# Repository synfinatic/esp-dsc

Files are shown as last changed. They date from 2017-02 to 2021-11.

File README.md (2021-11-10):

# ESP-DSC: Digital Setting Circles for ESP-12E/F

## About

Low cost alternative to my original Digital Setting Circles project the
[Teensy-DSC](https://github.com/synfinatic/teensy-dsc/).  This new design
uses the cheap ESP-12E/F WiFi enabled microcontroller which saves about 60% 
of the original price (~$40 vs ~$100).

I'm also planing to include the necessary .STL files so you can 3D print
the appropriate enclosure for the board.

More information about this project is available [on my website](https://synfin.net/sock_stream/tag/esp-dsc).

## v1.2 Status

 * Design PCB (complete!)
 * Port over the TeensyDSC code to the ESP-12 (complete!)
 * Verify that the ESP-12E is capable of handeling 2.5K PPR/10K count encoders (complete!)
 * Verify that the ESP-12E is capable of handeling 10K PPR/40K count encoders (failed!)
 * Create the necessary STL files to 3D print an enclosure for the board (complete!)
 * Major board change between v1.0 and v1.1- different pins used!

## v2.0 Status 
 * Redesign PCB for better performance  (TBD)
 * Update code based on new design (TBD)
 * Verify that the ESP-12E is capable of handeling 10k encoders (TBD)

## Performance

So a quick word about performance.  There are a number of people who claim that 
the ESP-12E has enough horsepower for two 2500PPR (10K after quadurature decoding) 
encoders.  One person told me they saw some errors, but they were small and 
likely caused by their mount.  This didn't seem very scientific to me, so I ran 
some tests.

My methodolgy is pretty simple.  I connected two ESP12E's to the same set of 
encoders.  Both ESP12E's used the same code and a custom modified version of 
[Paul Stoffgren's Encoder library](https://github.com/PaulStoffregen/Encoder) 
which has support for the ESP8266.  I also glued a toothpick to each encoder 
shaft to make it easier to rotate with my finger.  The test would be simple: If
both ESP12E's reported the same values, then I would say it was accurate.  But 
if the results were different, then it wasn't accurate.

I found that I could rotate a single 2,500PPR as fast as I possibly could 
without any error.  I could rotate a single 10,000PPR (40K after quadurature 
decoding) almost as fast without causing any error.

However, once I introduced a second encoder, I started seeing errors.  At about 
1 rotation/second, the 2500PPR encoders started to show some errors.  Two 
10,000PPR encoders had significant errors.  I also noticed that "flicking" the 
encoder causing it to quickly accellerate for a short duration (approx 1/4 
to 1/2 rotation) would cause significant errors even with the 2500PPR encoders.

This indicates that a person who does not very quickly move their scope 
should be able to use two 2500PPR encoders without introducing any 
errors.  If you're using a GoTo mount or a large scope you should be very 
safe.

I've done some testing on my AD12 (12" dobsonian) and 2500PPR/10,000 "count" 
encoders and found accuracy wasn't a problem at all.  The amount of error I saw
was approximagely +/-0.25deg meaning that if you have an EP with a 0.60deg 
effective FOV or more you should be able to use the ESP-DSC to point at an 
object and have it located inside your view through the scope.  Considering 
this is a mass produced dobsonian with a particile board mount, I consider 
this effectively within the error of the mount itself.

For comparison, my 30deg/82FOV Explore Scientific EP has an effective FOV of 
1.62deg in my scope which is more then twice the minimum.  

However I don't feel that it would be reliably accurate using 10,000PPR 
(40K count) encoders.  The result is I don't feel my initial PCB design is 
good enough with a single ESP12E.  I'm currently researching other solutions 
which could be implemented as cheaply and reliably as possible.

## Basic Features
I wanted to do my own digital setting circles (DSC) for my Apertura AD12.
The main goals were:

 * Support for at least 40K resolution via quadurature decoding (10k encoders)
 * Built in WiFi access point to allow wirelessly interfacing to an Apple iPad or Android tablet
 * Supporting at least [SkySafari Plus/Pro](http://www.skysafariastronomy.com/)
 * Powered via USB connection
 * Using industry standard RJ45 connection to encoders
 * Open source software & PCB design (GPLv3)
    * PCB Design done in [KiCad](http://www.kicad.org)
    * PCB's available from [OshPark](http://www.oshpark.com)
 * Inexpensive!  All the components should be available for < $40.

## Programming
You will need the Arduino 1.8.1+ IDE.   You will need to add support for the 
ESP8266 by [following the directions here](https://github.com/esp8266/Arduino).

Before you program your ESP-DSC you will need to:
 * Copy src/esp_dsc/config.h.sample to src/esp_dsc/config.h 
 * edit src/esp_dsc/config.h 

Under the tools menu, configure your board as follows:
 * Board: NodeMCU 1.0 (ESP-12E Module)
 * Flash Size: 4M (3M SPIFFS)
 * CPU Frequency: 80Mhz
 * Upload Speed: 115200 Baud

Do the following *exactly*:

 1. Disconnect the ESP-DSC from the encoders
 1. Connect a FTDI board to the FTDI header on the ESP-DSC and plug that into your computer
 1. Select the FTDI as your serial port in the Arduino IDE Tools menu
 1. Press and hold the Reset button
 1. Press and hold the Program button
 1. Release Reset button
 1. Release Program button
 1. Press the Upload button in the Arduino IDE Tools menu

## Supported Software

 * SkySafari Plus/Pro 
    - Select "Basic Encoder System"
    - Encoder Steps: Get Automatically
    - TCP Port 4030

## Similar Projects
There are a bunch of similar projects to ESP-DSC which you should be aware of:
 * [TeensyDSC](https://github.com/synfinatic/teensy-dsc/)
 * [Dave Ek's Setting Circles](http://eksfiles.net/digital-setting-circles/)
 * [mrosseel/arduino-dsc](https://github.com/mrosseel/arduino-dsc)
 * [mdw123/arduino-dsc](https://github.com/mdw123/arduino-dsc)
 * [Arduino Bluetooth DSC](http://orlygoingthirty.blogspot.com/2012/01/arduino-bluetooth-digital-setting.html)
 * [Mike Fulbright's Arduino DSC](http://msfastro.net/articles/arduinodsc/)
 * [Gigi's DSC w/ Magnetic Encoders](https://sites.google.com/site/gigimysite/home/astro/dsc-ekbox)

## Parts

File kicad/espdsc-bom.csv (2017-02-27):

Source | /Users/aturner/GIT/espdsc/kicad/espdsc.sch
Kicad Rev | Eeschema 4.0.5
Generated Date | Sunday | February 26 | 2017 'PMt' 03:40:56 PM
Title | Not Set
Company | Aaron Turner <synfinatic@gmail.com>
Revision | v0.1
Date Issue | 2017-02-25
Comment | https://synfin.net/XXXX
Reference | Value | Description | Availability | Package | MP | Price | Library | Library Ref
U1 | ESP-12E | ESP8266 | ESP-12E
J1 | RJ45 | conn | RJ45
P1 | USB_B | conn | USB_B
CONN1 | FTDI | synfinatic | FTDI
SW2 | Prog | switches | SW_SPST
SW1 | Reset | switches | SW_SPST
R4 | 1k | device | R
R3 | 1k | device | R
U3 | TXB0104 | 4-Bit Bidirectional Voltage-Level Translator with Auto Direction Sensing and +/-15 kV ESD Protect | Unavailable | None | TXB0104 | None | synfinatic | TXB0104
C1 | 1uf | device | C
C2 | 4.7uF | device | C
C3 | 1uF | device | C
U2 | MCP1825S-3302E/DB | MCP1825 |  | SOT-223-3 Microchip |  |  | synfinatic | MCP1825S-3302E/DB
JP1 | Jumper_NO_Small | device | Jumper_NO_Small

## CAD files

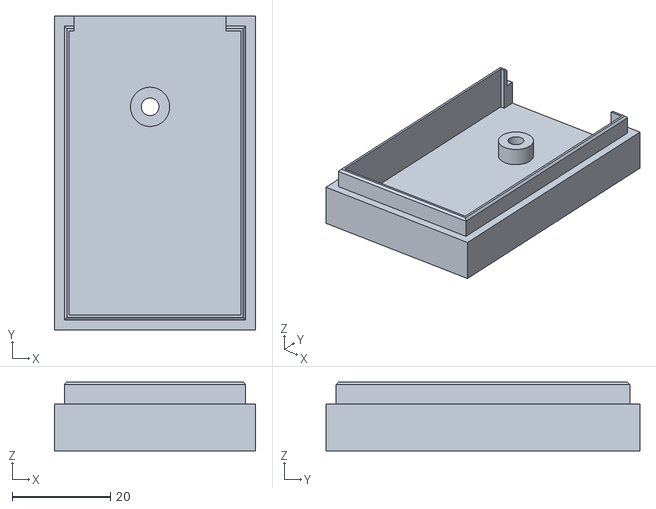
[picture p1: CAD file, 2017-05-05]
case/esp-dsc-v1-top.stl
41.0 x 64.0 x 14.0

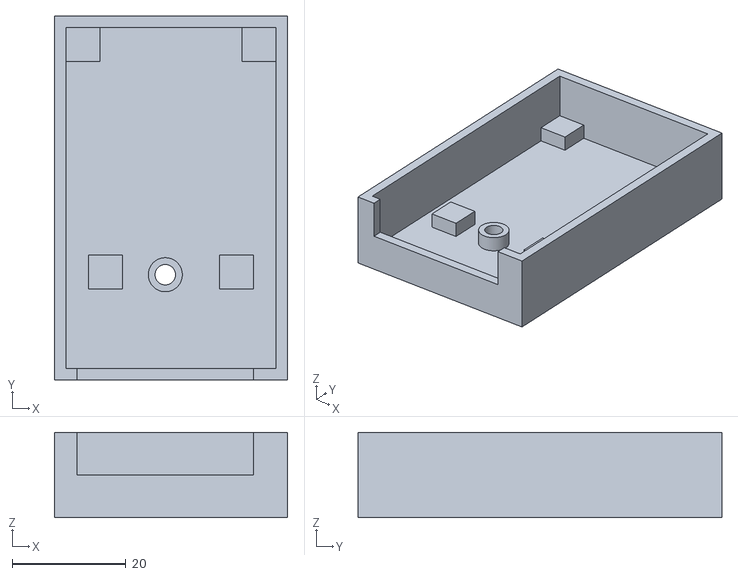
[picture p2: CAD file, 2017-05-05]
case/esp-dsc-v1-bottom.stl
41.0 x 64.0 x 15.0

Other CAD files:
case/esp-dsc-v1-case.f3d

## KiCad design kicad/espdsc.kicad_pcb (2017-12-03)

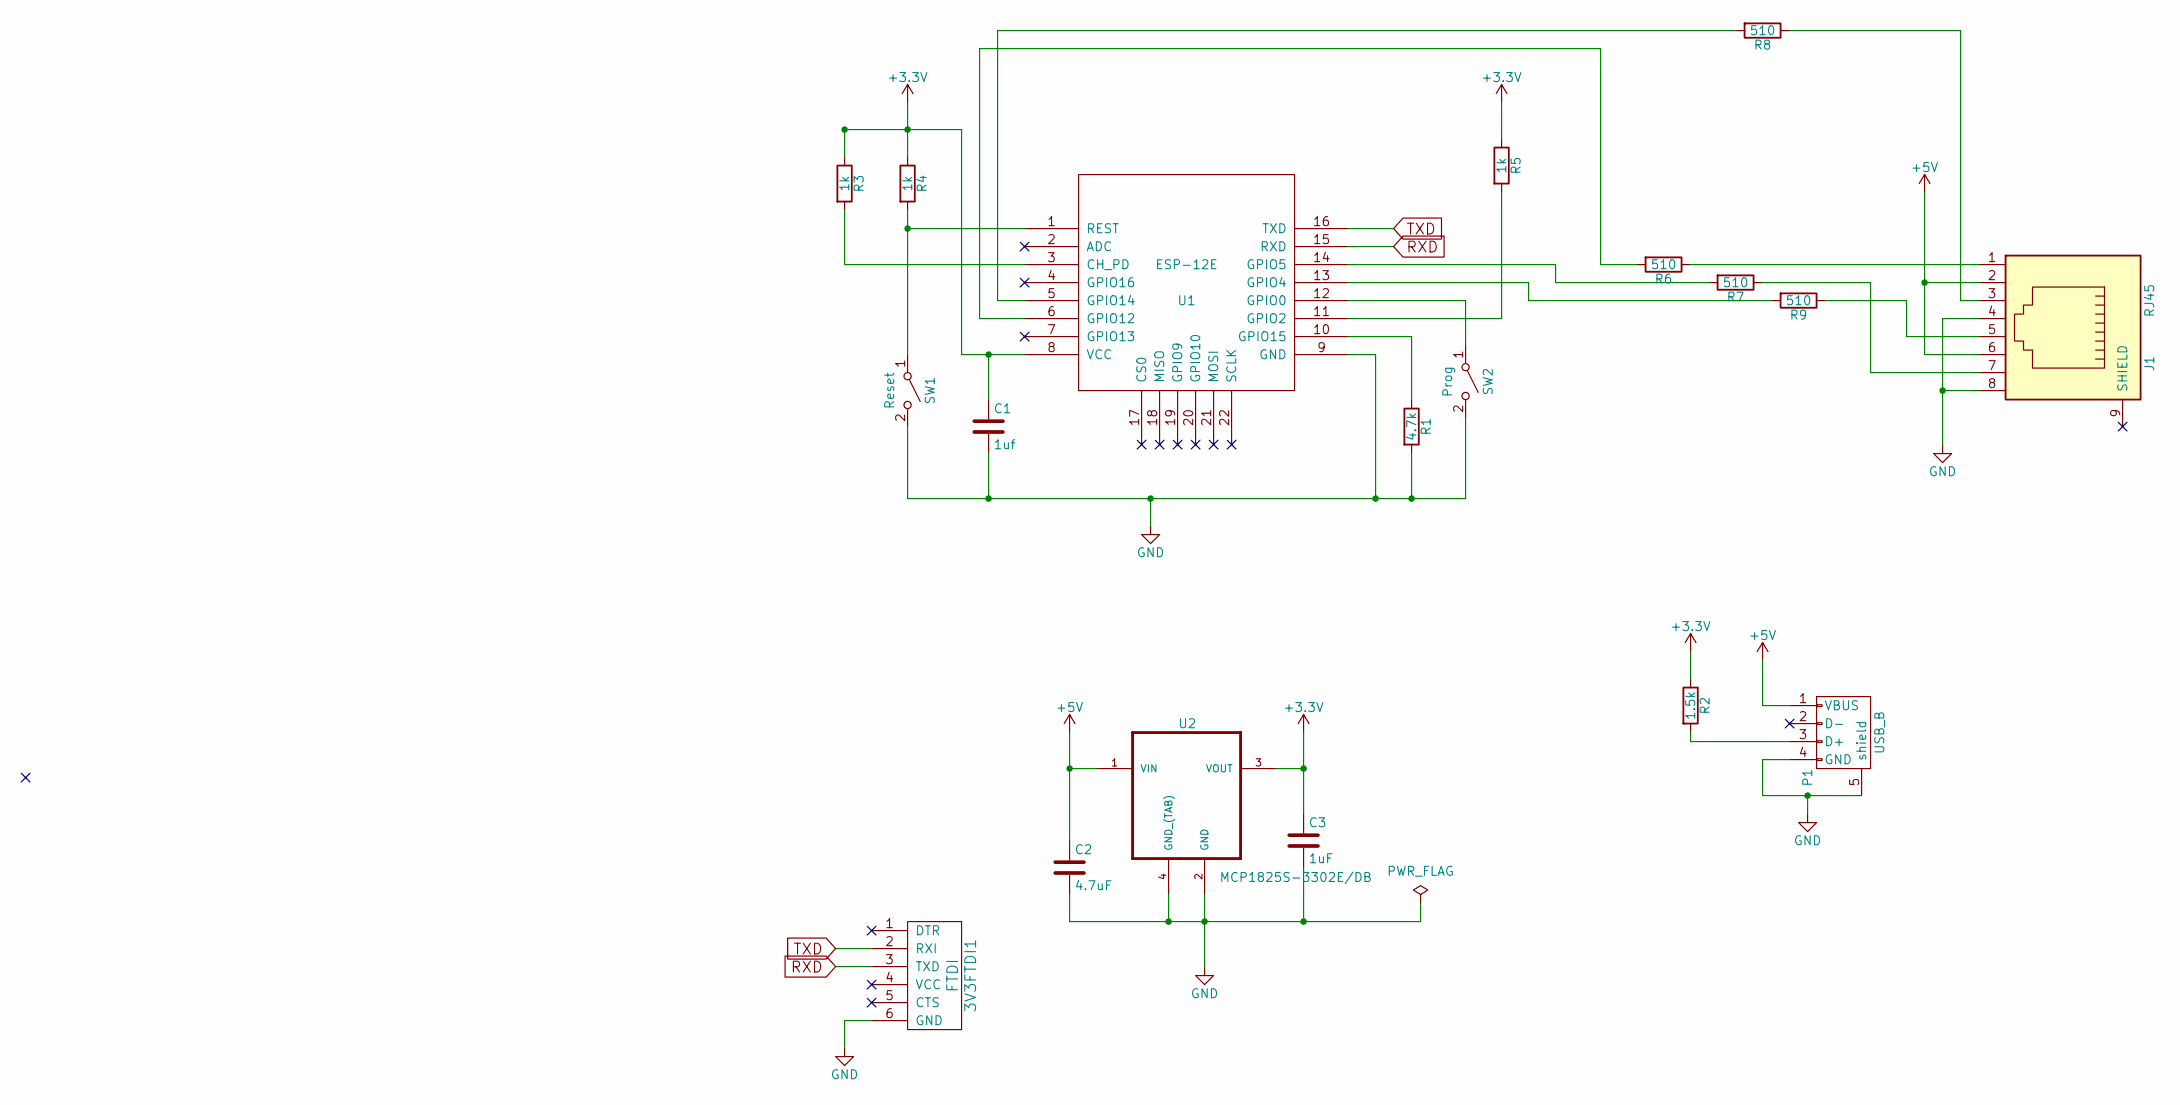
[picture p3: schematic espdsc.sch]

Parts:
3V3FTDI1: FTDI; FTDIHeader
C1: 1uf; C_0805_HandSoldering
C2: 4.7uF; C_0805_HandSoldering
C3: 1uF; C_0805_HandSoldering
J1: RJ45; RJ45_8
P1: USB_B
R1: 4.7k; R_0805_HandSoldering
R2: 1.5k; R_0805_HandSoldering
R3, R4, R5: 1k; R_0805_HandSoldering
R6, R7, R8, R9: 510; R_0805_HandSoldering
SW1: Reset; SPST-SMD-6x3.5
SW2: Prog; SPST-SMD-6x3.5
U1: ESP-12E; ESP-12E-SMD
U2: MCP1825S-3302E/DB; SOT-223

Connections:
+3V3: C1.1, C3.1, R2.1, R3.1, R4.1, R5.1, U1.8 (VCC), U2.3 (VOUT)
+5V: C2.1, J1.2, J1.6, P1.1 (VBUS), U2.1 (VIN)
GND: 3V3FTDI1.6 (GND), C1.2, C2.2, C3.2, J1.4, J1.8, P1.4 (GND), P1.5 (shield), R1.2, SW1.2 (B), SW2.2 (B), U1.9 (GND), U2.2 (GND), U2.4 (GND_(TAB))
unnamed: J1.1, R6.1
unnamed: J1.3, R8.1
unnamed: J1.5, R9.1
unnamed: J1.7, R7.1
unnamed: P1.3 (D+), R2.2
unnamed: R1.1, U1.10 (GPIO15)
unnamed: R3.2, U1.3 (CH_PD)
unnamed: R4.2, SW1.1 (A), U1.1 (REST)
unnamed: R5.2, U1.11 (GPIO2)
unnamed: R6.2, U1.6 (GPIO12)
unnamed: R7.2, U1.14 (GPIO5)
unnamed: R8.2, U1.5 (GPIO14)
unnamed: R9.2, U1.13 (GPIO4)
unnamed: SW2.1 (A), U1.12 (GPIO0)
RXD: 3V3FTDI1.3 (TXD), U1.15 (RXD)
TXD: 3V3FTDI1.2 (RXI), U1.16 (TXD)

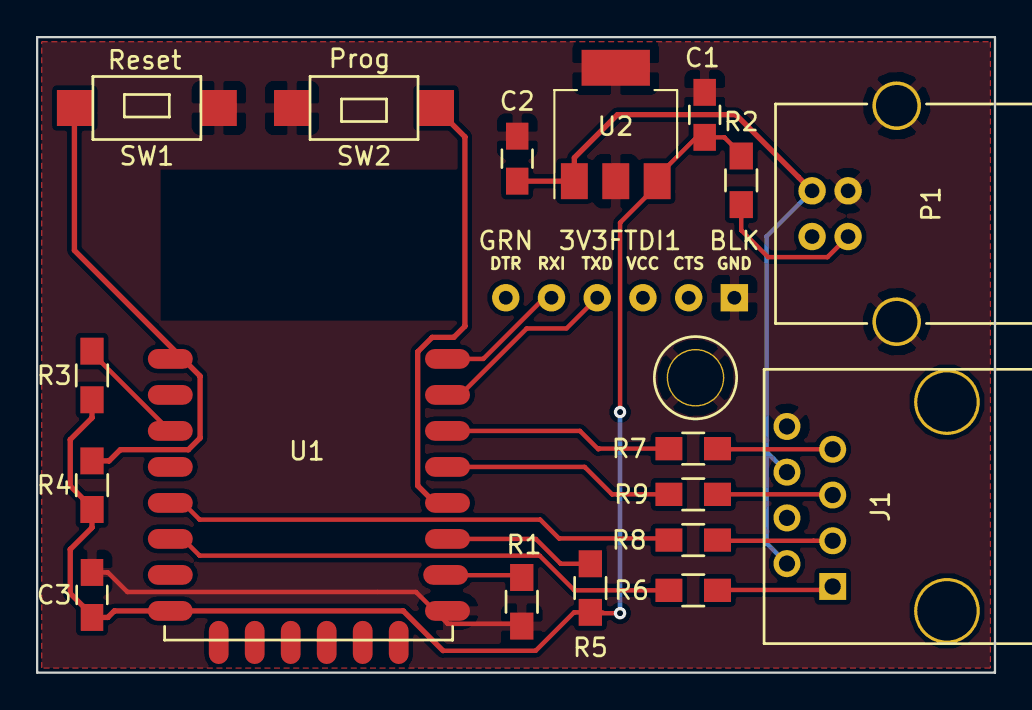
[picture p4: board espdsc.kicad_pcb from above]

Board: 2 copper layers, 53.2 x 35.3 mm, 19 parts (0 on the bottom side), 19 nets.

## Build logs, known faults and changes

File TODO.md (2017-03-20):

# v2.0.0 board:
 - Move RA-ChanA off pin 2 which conflicts with the onboard LED
 - Fix label on Reset Switch
 - Make board smaller
 - Improve programming reliability
    - https://blog.falafel.com/how-to-wire-the-esp8266-for-programming/
    - https://github.com/esp8266/Arduino/blob/master/doc/ESP_to_serial.png
 - Fix RJ45 mounting holes
 - Remove option of running power off FTDI board (ESP will crash on boot)
 - External pull up resitors for encoders?
 - May need to use LSI 7355R-S for encoders?
    - Provide SPI interface to avoid interrupts/polling.  
    - Need one per encoder ($4-6/ea)
    - Hard to find! (not Digikey/Newark/etc)
    - http://www.usdigital.com/products/interfaces/ics/LFLS7366R-S
    - http://www.omnipro.net/lsi-csi/LS7366R-S
    - http://www.anaheimautomation.com/products/ics/lsi-csi-item.php?sID=270&serID=17&pt=i&tID=159&cID=55
    - Notes:
        - http://www.micromouseonline.com/2008/02/21/ls7366-quadrature-counter/
        - http://hades.mech.northwestern.edu/index.php/Using_the_LS7366R_SPI_Quadrature_Counter

# Software
 - Fix interrupt handler to not miss clicks
 - use WiFiManager library
 - Save encoder resolution to flash
 - Investigate webserver for config
 - Display MAC address for DHCP hard coding
 - Improve use of DEBUG

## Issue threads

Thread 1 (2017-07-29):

encoder.h is missing

ajaisehgal, 2017-07-29:
@synfinatic esp_dsc.ino includes Encoder.h which does not appear to be checked into the source.  Ok read in your testing code that I need to use https://github.com/PaulStoffregen/Encoder.  Maybe should be in the readme.

synfinatic, 2017-07-29:
Intended.  You should install the [Encoder library](https://github.com/PaulStoffregen/Encoder) either manually or via the Arduino IDE

Closed 2017-07-29.

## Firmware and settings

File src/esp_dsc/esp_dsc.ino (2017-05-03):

/*
 * ESP-12E/F Digital Setting Circles
 * Copyright (C) 2017 Aaron Turner
 *
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
 */

#include <Arduino.h>
#include "esp_dsc.h"
#include "dsc.h"
#include "utils.h"

#define ENCODER_OPTIMIZE_INTERRUPTS
#include <Encoder.h>
Encoder EncoderRA(CHAN_RA_A, CHAN_RA_B);
Encoder EncoderDEC(CHAN_DEC_A, CHAN_DEC_B);

#include <ESP8266WiFi.h>
#include <WiFiClient.h>
WiFiServer server(TCP_PORT);
WiFiClient serverClients[MAX_SRV_CLIENTS];
void process_client(uint8_t c);

long RA_Res = RA_RESOLUTION;
long DEC_Res = DEC_RESOLUTION;


void
setup() {
    uint8_t i = 0;
    Serial.begin(SERIAL_SPEED);

#ifdef DEBUG
    pinMode(0, INPUT_PULLUP);
#endif

#ifdef ENABLE_WIFI
    Serial.println("Starting up WiFi...");
#ifdef AP_MODE
    WiFi.disconnect(true);
    WiFi.mode(WIFI_AP_STA);
    WiFi.softAP(WIFI_SSID, WIFI_PASSWORD);
#else
    WiFi.begin(WIFI_SSID, WIFI_PASSWORD);
    while (WiFi.status() != WL_CONNECTED) {
        Serial.print("Waiting for WiFi status to go live...\n");
        delay(500);
    }
    Serial.printf("Connected to %s!\n", WIFI_AP);
#endif
    server.begin();
    server.setNoDelay(true);
//     Serial.printf("Connect to %s:%d\n", WiFi.localIP(), TCP_PORT);
#else
    Serial.println("WiFi disabled!");
#endif // ENABLE_WIFI

}


#ifdef ENABLE_WIFI
/*
 * Process TCP client request on the given serverClient entry
 */
void
process_client(uint8_t c) {
    char buff[CLIENT_BUFF_LEN];
    char *value;
    char val = serverClients[c].read();
    long ra_value, dec_value;;
    int i, j;
    switch (val) {
        // get encoder values
        case 'Q':
            ra_value = EncoderRA.read();
            dec_value = EncoderDEC.read();
            value = EncoderValue(ngc_convert_encoder_value(ra_value, RA_Res), true);
            sprintf(buff, "%s\t", value);
            value = EncoderValue(
                    ngc_convert_encoder_value(dec_value, DEC_Res), true);
            serverClients[c].printf("%s%s\r\n", buff, value);
            break;
        case 'R':
            // set resolution
            memset(buff, '\0', CLIENT_BUFF_LEN);
            i = 0;
            j = 0;
            // Horrible hack around ESP8266 not having sscanf()
            if (serverClients[c].available()) {
                serverClients[c].read(); // read the space
            } else {
                Serial.printf("short command!\n");
                return;
            }

            while (i < 2) {
                while (serverClients[c].available() && serverClients[c].peek() != ' ') {
                    if (serverClients[c].peek() != ' ') {
                        buff[j] = serverClients[c].read();
                        j++;
                    }
                }
                if (i == 0) {
                    j = 0;
                    ra_value = String(buff).toInt();
                    Serial.printf("RA = %ld\n", ra_value);
                    memset(buff, '\0', CLIENT_BUFF_LEN);
                    serverClients[c].read(); // read the space
                } else {
                    dec_value = String(buff).toInt();
                    Serial.printf("DEC = %ld\n", dec_value);
                }
                i++;
            }
            if (i != 2) {
                Serial.printf("Unable to process: R %s\n", buff);
                return;
            }
            RA_Res = ra_value;
            DEC_Res = dec_value;
            break;
        case 'G':
        case 'H':
            // get resolution
            long ra, dec;
            char ra_pos[2], dec_pos[2];

            ra = abs(RA_Res);
            dec = abs(DEC_Res);

            ra_pos[1] = dec_pos[1] = '\0';
            ra_pos[0] = ra == RA_Res ? '+' : '-';
            dec_pos[0] = dec == DEC_Res ? '+' : '-';

            Serial.printf("%s%05ld\t%s%05ld\r\n", ra_pos, RA_Res, dec_pos, dec); 
            serverClients[c].printf("%s%05ld\t%s%05ld\r\n", ra_pos, RA_Res, dec_pos, dec); 
            break; 
        case 'V':
        case 'v':
            // get version
            serverClients[c].printf("ESP-DSC v%s\n", ESP_DSC_VERSION);
            break;
        default:
            Serial.printf("Unknown command: %c\n", val);
    }
}
#endif // ENABLE_WIFI


void 
loop()
{ 
    static unsigned long last = 0;
    unsigned long now = millis();
    uint8_t c;
    long dec_value, ra_value;
    char buffer[50], ra_f[10], dec_f[10];
#ifdef ENABLE_WIFI
    // look for new clients
    if (server.hasClient()) {
        for (c = 0; c < MAX_SRV_CLIENTS; c++) {
            // find a free slot
            if (!serverClients[c] || !serverClients[c].connected()) {
                if (serverClients[c]) 
                    serverClients[c].stop();
                serverClients[c] = server.available();
                continue;
            }
        }
        
        // no free slots to reject
        WiFiClient serverClient = server.available();
        serverClient.stop();
    }

    // check clients for data
    for (c = 0; c < MAX_SRV_CLIENTS; c++) {
        if (serverClients[c] && serverClients[c].connected()) {
            if (serverClients[c].available()) {
                process_client(c);
            }
        }
    }
#endif // ENABLE_WIFI

#ifdef DEBUG
    if ((now - last) >= SERIAL_PRINT_DELAY) {
        last = now;
        if (LOW == digitalRead(0)) {
            // zero out encoder values for testing
            noInterrupts();
            EncoderRA.write(0);
            EncoderDEC.write(0);
            interrupts();
        }
        ra_value = EncoderRA.read();
        dec_value = EncoderDEC.read();
        snprintf(buffer, 100,
                "RA Ticks: %ld\tRevs: %s\nDec Ticks: %ld\tRevs: %s\n",
                ngc_convert_encoder_value(ra_value, RA_Res),
                ftoa(ra_f, ra_value/(float)RA_Res, 3),
                ngc_convert_encoder_value(dec_value, DEC_Res),
                ftoa(dec_f, dec_value/(float)DEC_Res, 3));
        Serial.print(buffer);
    }
#endif
    delay(25); // service WiFiClient
}

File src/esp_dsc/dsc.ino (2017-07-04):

/*
 * Teensy 3.1 Digital Setting Circles
 * Copyright (C) 2014-2015 Aaron Turner
 *
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
 */

// Don't include anything else or problems running unit tests!
#include "dsc.h"
#include <Arduino.h>


/*
 * Looks like NGC uses 16bits to store the encoder value.
 * So depending on the resolution, it either returns a 
 * uint16_t value or int16_t value.
 *
 * So if you have an abs(resolution) < 2^15, then the range is:
 * -resolution/2 to (resolution/2-1)
 *
 * If your resolution is larger, then the range is:
 * 0 to 2^16-1
 *
 * It's so far undocumented how encoders mounted backwards
 * with a negative resolution should be handled for the
 * latter situation.  I decided to do the semi-obvious thing
 * of counting backwards.
 */
int32_t
ngc_convert_encoder_value(int32_t encoder, long resolution) {
    int32_t ret = 0;
    static int32_t half_res = resolution / 2;

    // Different math if resolution can be stored in int16_t
    if ((resolution < INT16_MAX) && (resolution >= INT16_MIN)) {
        if (resolution >= 0) {
            encoder = encoder % resolution;
            if (encoder >= 0) {
                if (encoder <= (half_res -1)) {
                    ret = encoder;
                } else {
                    ret = -half_res - (half_res - encoder);
                }
            } else {
                // encoder is negative
                if (abs(encoder) <= half_res) {
                   ret = encoder;
                } else {
                    ret = half_res + (half_res + encoder);
                }
            }
        } else {
            encoder = encoder % abs(resolution);
            // resolution is negative
            if (encoder >= 0) {
                if (encoder <= abs(half_res)) {
                    ret = -encoder;
                } else {
                    ret = abs(half_res) - (encoder % abs(half_res));
                }
            } else {
                if (abs(encoder) < abs(half_res)) {
                    ret = -encoder;
                } else {
                    ret = half_res + (half_res - encoder);
                }
            }
        }
    } else {
        if (resolution > 0) {
            if (encoder >= 0) {
                ret = encoder % resolution;
            } else {
                ret = (resolution + (encoder % resolution)) % resolution;
            }
        } else {
            // resolution is negative
            if (encoder >= 0) {
                ret = (-resolution - (encoder % resolution)) % -resolution;
            } else {
                ret = ((encoder * -1) % resolution) % resolution;
            }
        }
    }
    return ret;
}

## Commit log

2017-02-27 v1.0 design
    Completely untested.
    [espdsc.kicad_pcb, espdsc.sch]
2017-03-17 update design for v1.0 release
    [espdsc-bom.csv, espdsc.kicad_pcb, espdsc.sch]
2017-03-18 First pass at encoder decoding
    POC for using interrupts and global volatile variables. Code seems
    to at first glance work and seems to be able to accurately track
    two 2.5 (native)/10K (quadrature) encoders
2017-03-19 Working, basic bench tested code
    - Doesn't support setting the encoder resolution (yet)
    - Seems to handle both interrupts and the WiFi just fine
    - Supports both SoftAP and Client mode!
    [dsc.ino, esp_dsc.ino, utils.ino]
2017-03-19 Major code improvements & docs
    - Improve docs for users
    - Add more commands (get version, get/set resolution of encoders)
    - Move local config to config.h
2017-03-19 Fix encoder pins & optimize interrupts
    - The RA/Dec pins were swapped
    - Try to optimize handing of interrupts. Testing with 2.5k CPR encoders
    shows that I wasn't fully sucessful yet.
    [esp_dsc.ino]
2017-03-20 more optimizations (which don't work)
    Saving this mostly for posterity as even after removing (most of) the
    digitalRead() calls, we can't keep up with 2 encoders. Going to need
    to investigate alternatives documented in TODO.md
2017-03-26 Add support for Encoder library and better debugging
2017-05-03 Basic working code
    Remove all the crap that we don't need anymore since we're done testing
    different methods of trying to keep up with the newer high resolution
    encoders (above 2500PPR/10K "count"). This just uses the Encoder
    library which is stable and works well.
    Code has been tested using my telescope and seems to work great with
    SkySafari!
2017-05-05 Add STL and Fusion360 case files for v1.0 case
    [esp-dsc-v1-bottom.stl, esp-dsc-v1-case.f3d, esp-dsc-v1-top.stl]
2017-07-04 fixes for neg encoder resolution
    merged from TeensyDSC
    [dsc.ino]
2017-12-03 v1.1 board & code
    - Move GPIO2/15 to GPIO14/12 to avoid boot conflict
    - Remove level shifter and replace with 4x 150Ohm resistors
    - Tweak RJ45 footprint for better fit
    - Add pullup for D+ on USB
    - Remove 3.3V FTDI jumper
    - Move Reset button label
    - FTDI no longer can provide power
    [espdsc.kicad_pcb, espdsc.sch]
2017-12-03 v1.2
    - Switch ESP12E to pure SMD footprint
    [espdsc.kicad_pcb, espdsc.sch]
2021-11-10 Update README.md
    https://forum.kicad.info/t/warning-avoid-all-links-to-kicad-pcb-org-use-kicad-org/31521

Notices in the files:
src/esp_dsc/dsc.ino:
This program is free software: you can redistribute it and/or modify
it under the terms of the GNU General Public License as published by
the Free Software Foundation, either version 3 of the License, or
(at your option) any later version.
